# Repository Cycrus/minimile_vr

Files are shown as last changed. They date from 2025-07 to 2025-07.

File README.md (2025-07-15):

<div align="center">
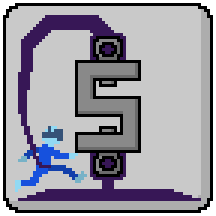
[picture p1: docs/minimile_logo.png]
SlimStep VR Logo
  
  <h1>SlimStep VR</h1>
  <h2>A Minimal, low-cost DIY VR treadmill system</h2>
</div>

<div align="center">
  
  
  
  
</div>

## What is SlimStep VR?
SlimStep VR is an answer to the demand for more affordable immersion enhancing VR devices. It is a minimal, low-cost VR treadmill system, which allows for more immersive smooth movement in Steam VR applications than a controller can provide.

You can mount the system to a wall or another sturdy part of your playspace. A rubber rope then connects your waist with the mounting point holding you approximately in space, while a sensor measures how much force you use to walk or run away from the mounting point. In addition to a slippery floor - or simply with wearing wool socks - the setup offers a rather immersive walking/running experience.

The system currently works unidirectional in the forward direction. In the current version there is no directional information implemented (left or right motion).

SlimStep VR is currently under active development.

## Installation
Installation requires setting up the driver software on your PC and setting up the hardware.

### Installing OpenVR Driver
The OpenVR driver is required for SteamVR to detect the device as an input option for VR games. Simply double click the file "install_driver.bat" in the folder "openvr_driver". It just takes an instant and the driver is installed.

If you want to uninstall the driver, there is a file named "uninstall_driver.bat" in the same folder.

> **WARNING**  
> In the current version it is important, that you uninstall the driver before you remove or relocate the project directory. Otherwise there will be some driver leftovers in the Steam registry, which could lead to undefined behavior. In all cases you can remove the driver with "<steam-directory>/steamapps/common/SteamVR/bin/win64/Vrpathreg.exe". Run it in the console with "show" as an argument to check the full path of the left-over driver, then run it with the argument "removedriver <full-driver-path>" to remove the left-over driver.

### Setting Up the Hardware
The more involved step is building the hardware of the system. You will need the following components. The links are links of the products I used for my own design.

- [50 kg load cell](https://www.amazon.de/dp/B077YLHG9D) (S-shape to measure pull forces, not push)
- Arduino (any type will do; I used an Arduino Nano Every) - For measuring the movement forces - Sends the load cell output to the PC
- [HX711 load cell module](https://www.amazon.de/dp/B0DJX8BPQL) - Required to read out the load cell
- [Tensioning belt](https://www.amazon.de/dp/B0DRNBRWLL) - Keeps you briefly in place while moving

<div align="center">
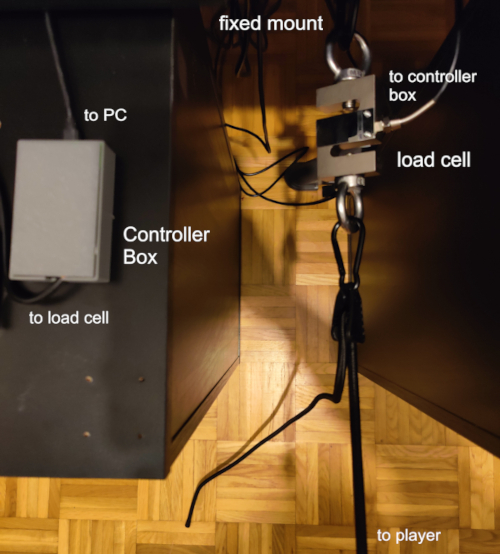
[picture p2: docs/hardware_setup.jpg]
Hardware Setup
  
</div>

For my design I used 2 M12 eyebolts and 2 carabiners to hang the load cell between my desk and the tensioning belt. I then knotted together the other end of the belt with some terry cloth to create a soft belt around my hip.

Now you need to wire the electrical components together as in the following image.

<div align="center">
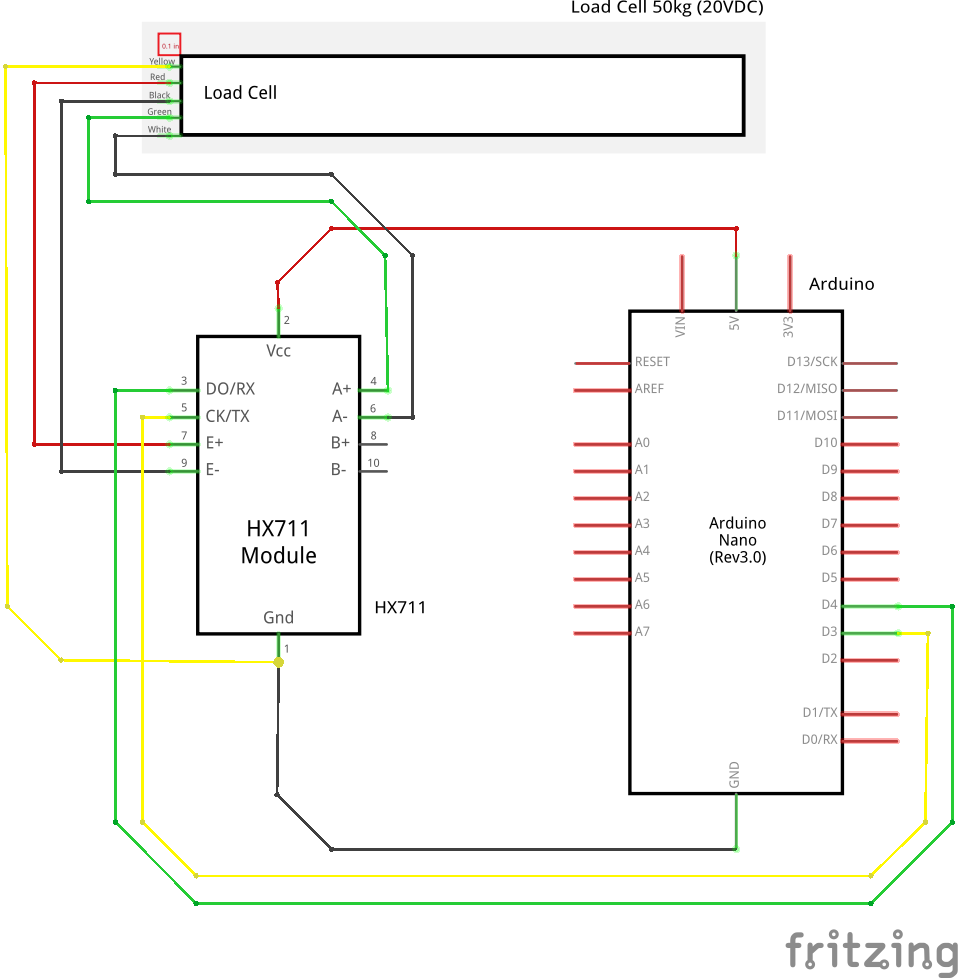
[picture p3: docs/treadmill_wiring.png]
Wiring
  
</div>

- Red wire: E+
- Black wire: E-
- Yellow wire: GND
- Green wire: S+/A+
- White wire: S-/A-

The HX711 then needs to be supplied with 5V from the Arduino. Connect its CLK (yellow) with D3 and its Data Out (green) with S4.

I used a 20VDC load cell to connect to my 5V excitation supply, wich worked perfectly fine.

After wiring everything, connect the Arduino to your PC with an USB cable. Now you need to upload the Arduino sketch "load_cell_module/load_cell_module.ino" to the Arduino. I suggest you use the official [Arduino IDE](https://www.arduino.cc/en/software/) for that. Compilation requires the HX711 Arduino library by Rob Tillaart.

> **Note**
> Additionally, the path "load_cell_module\case contains" stl and sliced gcode files to 3d-print a small case for the controllers. The lid of the case can be placed with double sided tape.

## Project Structure (Folders)
    - docs: Images of the project setup, wiring, etc.
    - load_cell_module: Contains everything regarding hardware.
      - case: Files for printing the case for the Arduino Nano and teh HX711 module
      - validation: Some Python scripts for validating the treadmill device
    - openvr_driver: Contains everything regarding the driver software.
      - CustomTreadmillDriver: The driver in its release shape
      - openvr_treadmill_driver_src: The source code of the treadmill driver

## References
  - OpenVR SteamVR driver documentation - https://github.com/ValveSoftware/openvr/wiki/Driver-Documentation
  - Finallyfunctionals OpenVR driver example - https://github.com/finallyfunctional/openvr-driver-example/tree/main

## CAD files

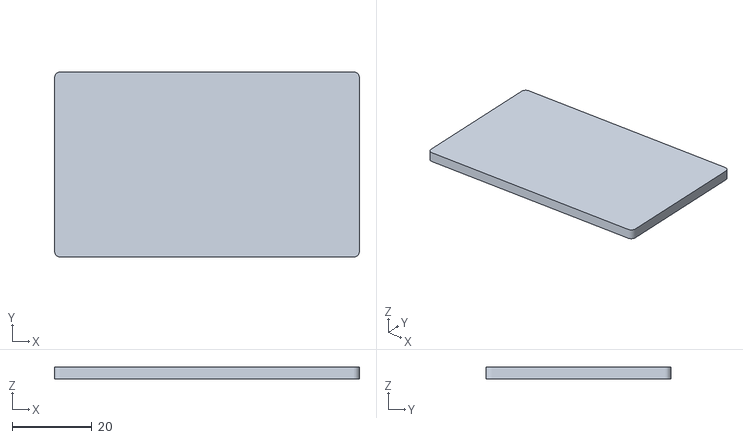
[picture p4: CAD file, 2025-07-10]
load_cell_module/case/treadmill_controller_case_top.stl
76.4 x 46.4 x 3.00

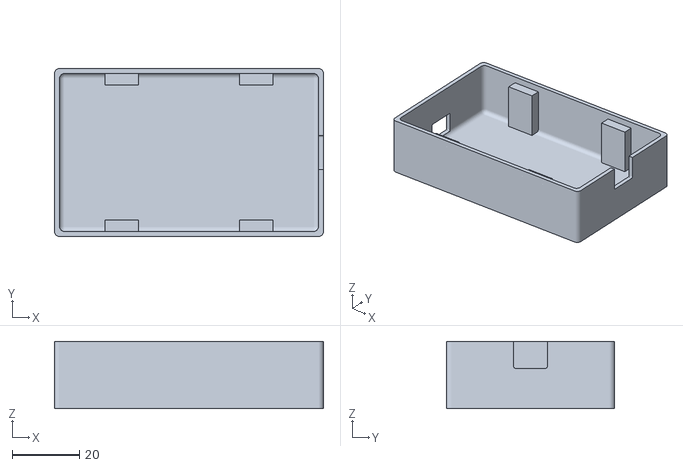
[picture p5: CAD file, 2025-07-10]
load_cell_module/case/treadmill_controller_case_bottom.stl
80.0 x 50.0 x 20.0

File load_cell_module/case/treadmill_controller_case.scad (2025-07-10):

// More information: https://danielupshaw.com/openscad-rounded-corners/

// Set to 0.01 for higher definition curves (renders slower)
$fs = 0.15;

module roundedcube(size = [1, 1, 1], center = false, radius = 0.5, apply_to = "all") {
	// If single value, convert to [x, y, z] vector
	size = (size[0] == undef) ? [size, size, size] : size;

	translate_min = radius;
	translate_xmax = size[0] - radius;
	translate_ymax = size[1] - radius;
	translate_zmax = size[2] - radius;

	diameter = radius * 2;

	obj_translate = (center == false) ?
		[0, 0, 0] : [
			-(size[0] / 2),
			-(size[1] / 2),
			-(size[2] / 2)
		];

	translate(v = obj_translate) {
		hull() {
			for (translate_x = [translate_min, translate_xmax]) {
				x_at = (translate_x == translate_min) ? "min" : "max";
				for (translate_y = [translate_min, translate_ymax]) {
					y_at = (translate_y == translate_min) ? "min" : "max";
					for (translate_z = [translate_min, translate_zmax]) {
						z_at = (translate_z == translate_min) ? "min" : "max";

						translate(v = [translate_x, translate_y, translate_z])
						if (
							(apply_to == "all") ||
							(apply_to == "xmin" && x_at == "min") || (apply_to == "xmax" && x_at == "max") ||
							(apply_to == "ymin" && y_at == "min") || (apply_to == "ymax" && y_at == "max") ||
							(apply_to == "zmin" && z_at == "min") || (apply_to == "zmax" && z_at == "max")
						) {
							sphere(r = radius);
						} else {
							rotate = 
								(apply_to == "xmin" || apply_to == "xmax" || apply_to == "x") ? [0, 90, 0] : (
								(apply_to == "ymin" || apply_to == "ymax" || apply_to == "y") ? [90, 90, 0] :
								[0, 0, 0]
							);
							rotate(a = rotate)
							cylinder(h = diameter, r = radius, center = true);
						}
					}
				}
			}
		}
	}
}

length = 80.0;
width = 50.0;
height = 20.0;
wall_thickness = 1.5;

mount_length = 10.0;
mount_width = 5.0;

loadcell_cutout_z_offset = 17.0;
loadcell_cutout_width = 10.0;
loadcell_cutout_height = 10.0;

usb_y_offset = 0.0;
usb_z_offset = 6.0;
usb_width = 10.0;
usb_height = 7.0;

// Box
module box_shape()
{
    union()
    {
        difference()
        {
            roundedcube([length, width, height], center = true,
                        apply_to = "xy",
                        radius = 1.5);
            translate([0, 0, wall_thickness])
            {
                roundedcube([length - 2 * wall_thickness,
                             width - 2 * wall_thickness,
                             height], center = true,
                             apply_to = "zmin",
                             radius = 1.5);
            }
        }
        for (sx = [-1, 1], sy = [-1, 1]) {
            translate([sx * length / 4, sy * width / 2 - sy * mount_width / 2 , 0])
                cube([mount_length, mount_width, height - wall_thickness*3], center = true);
        }
    }
}

module loadcell_cutout()
{
    translate([length / 2 + 0.1, 0, -height / 2 + loadcell_cutout_z_offset])
    {
        roundedcube([wall_thickness * 4, loadcell_cutout_width, loadcell_cutout_height], apply_to = "x", center = true);
    }
}

module usb_cutout()
{
    translate([-length / 2 - 0.1, usb_y_offset, -height / 2 + usb_z_offset])
    roundedcube([wall_thickness * 4, usb_width, usb_height], center = true);
}

// Box
difference()
{
    box_shape();
    loadcell_cutout();
    usb_cutout();
}

// Top
%translate([0, 0, 9])
{
roundedcube([length - wall_thickness*2.4, width - wall_thickness*2.4
    , 3], center = true,
                        apply_to = "xy",
                        radius = 1.5);
}

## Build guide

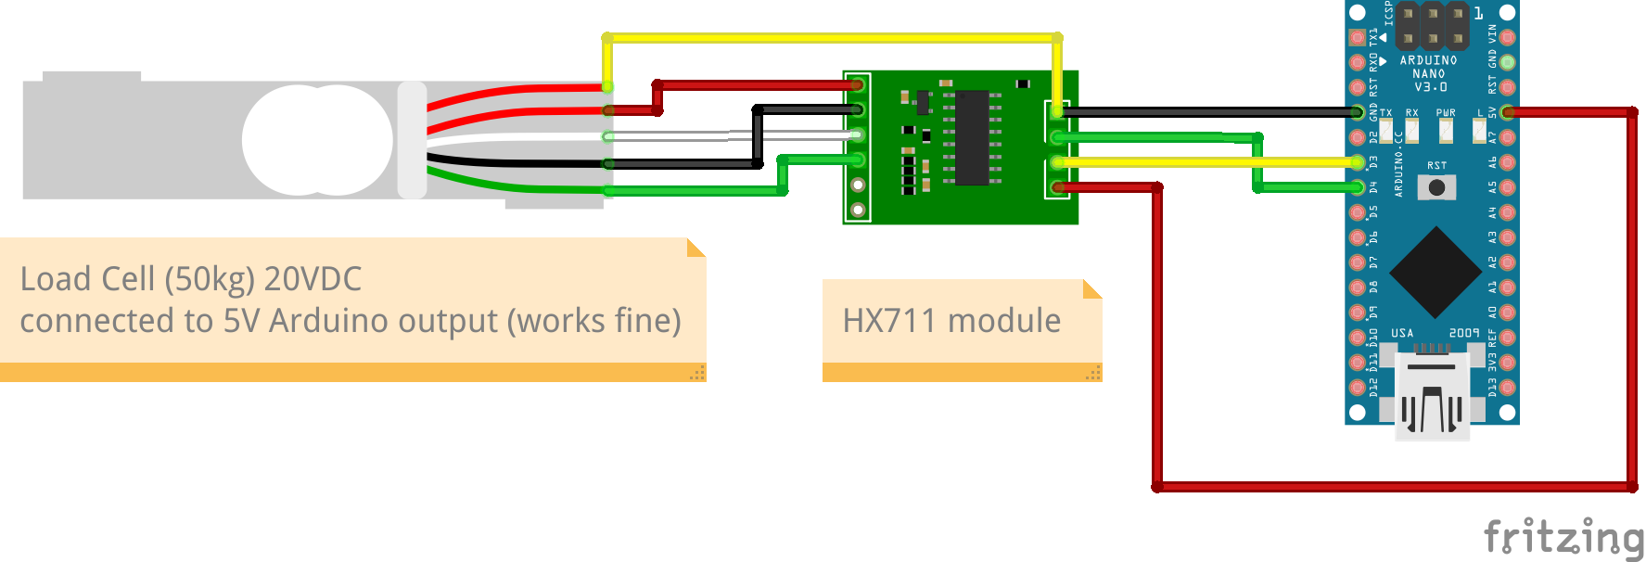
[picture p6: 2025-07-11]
docs/treadmill_wiring_bb.png

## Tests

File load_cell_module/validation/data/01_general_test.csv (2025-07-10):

value
0.00
35.00
26.00
2.00
17.00
15.00
-13.00
-33.00
-18.00
-3.00
-19.00
5.00
14.00
-4.00
-7.00
-10.00
-35.00
-15.00
-10.00
-8.00
0.00
4.00
32.00
43.00
-15.00
-25.00
-19.00
-16.00
-35.00
-64.00
-46.00
10.00
-22.00
-31.00
-14.00
77.00
439.00
1065.00
495.00
-824.00
-1617.00
-1998.00
-2334.00
-2769.00
-3097.00
-2827.00
-2540.00
-2337.00
-2412.00
-2186.00
-2198.00
-2547.00
-2710.00
-3399.00
-4373.00
-3023.00
-2238.00
-3049.00
-3018.00
-2490.00
-2810.00
80.00
1455.00
1559.00
3263.00
3301.00
2088.00
4641.00
4975.00
2108.00
1059.00
-1908.00
-4612.00
-5271.00
-7295.00
-7231.00
-6870.00
-6267.00
-5292.00
-4180.00
-2882.00
-2643.00
-2982.00
-3117.00
-4601.00
-6488.00
-6737.00
-7783.00
-8676.00
-8621.00
-8859.00
-8740.00
-8734.00
-8913.00
-8930.00
-8680.00
-8216.00
-7729.00
-6983.00
-6696.00
-6656.00
-6592.00
-6754.00
-6963.00
-6964.00
-7809.00
-7993.00
-9077.00
-9466.00
-9735.00
-9764.00
-9604.00
-9544.00
-9129.00
-8819.00
-8754.00
-8522.00
-9139.00
-7935.00
-8011.00
-11576.00
-7694.00
-8236.00
-9470.00
-7908.00
-7213.00
-8636.00
-8092.00
-7064.00
-7049.00
-8079.00
-8161.00
-6518.00
-6736.00
-6827.00
-2557.00
-451.00
-1514.00
-1429.00
-1541.00
-3830.00
-3453.00
-4963.00
-4793.00
-5316.00
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

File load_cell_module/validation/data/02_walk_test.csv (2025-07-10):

value
-14.00
-15.00
53.00
7.00
-12.00
-15.00
-45.00
-27.00
2.00
48.00
55.00
23.00
51.00
46.00
-3.00
-4.00
-14.00
-55.00
-55.00
-52.00
9.00
31.00
2.00
-45.00
-34.00
-6.00
-13.00
-22.00
0.00
260.00
632.00
-8.00
-913.00
-1611.00
-2084.00
-2106.00
-2388.00
-3052.00
-2974.00
-2841.00
-3042.00
-2882.00
-2803.00
-2604.00
-2186.00
-2153.00
-2348.00
-2504.00
-2582.00
-2905.00
-2692.00
-2600.00
-2307.00
-3057.00
-5327.00
-7311.00
-6559.00
-5712.00
-6253.00
-8525.00
-8853.00
-7943.00
-8183.00
-8823.00
-8697.00
-7994.00
-7712.00
-6903.00
-7422.00
-9762.00
-7546.00
-5891.00
-6654.00
-8743.00
-7648.00
-6544.00
-7664.00
-8819.00
-7574.00
-7007.00
-7799.00
-8067.00
-7525.00
-7535.00
-7672.00
-7560.00
-7538.00
-7728.00
-7942.00
-8686.00
-9037.00
-8134.00
-8174.00
-8629.00
-7991.00
-7664.00
-7329.00
-6944.00
-7419.00
-7073.00
-5211.00
-5563.00
-6883.00
-6468.00
-8279.00
-8617.00
-8981.00
-9838.00
-9718.00
-8495.00
-10633.00
-8546.00
-8340.00
-8839.00
-8569.00
-8444.00
-9026.00
-9423.00
-9526.00
-9997.00
-9914.00
-9331.00
-8983.00
-8756.00
-8568.00
-8645.00
-8653.00
-8599.00
-8131.00
-7610.00
-7116.00
-6466.00
-6208.00
-5356.00
-5271.00
-5100.00
-5643.00
-5402.00
-5853.00
-6207.00
-6650.00
-6748.00
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

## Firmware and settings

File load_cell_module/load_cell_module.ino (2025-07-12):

/**
 * The software running on the Arduino controlling the load cell.
 * Produces a 10 Hz output signal between 0 and 1 indicating how
 * string the load cell was pulled. This signal is interpreted
 * as different speeds of moving forward.
 * 
 * Compilation requires the HX711 Arduino library by Rob Tillaart.
 * The CLK pin of the HX711 is wired to digital 3 and the data output
 * is wired to digital 4 of the Arduino.
 */

#include "HX711.h"

uint8_t data_pin  = 4;
uint8_t clock_pin = 3;
HX711 treadmill;

float raw_measurement(float value)
{
  return value;
}

float ema_measurement(float value, float alpha)
{
  static float result = NAN;
  if(isnan(result))
  {
    result = value;
  }
  else
  {
    float prev_result = result;
    result = alpha * value + (1 - alpha) * prev_result;
  }
  return result;
}

float normalize_measurement(float value, float min_value, float max_value)
{
  float result = (value - min_value) / (max_value - min_value);
  if(result > 1.0)
    result = 1.0;
  else if(result < 0.0)
    result = 0.0;
  return result;
}


void setup()
{
  treadmill.begin(data_pin, clock_pin);
  Serial.begin(9600);
  while(!Serial) {}
  treadmill.set_scale();
  treadmill.tare();
}

void loop()
{
  float raw_value = treadmill.get_units();
  /*
  This is an active decision against smoothing. A useful EMA smoothing would lead
  to too much latency for a useful game input device.
  */
  // float smoothed_value = ema_measurement(raw_value, 0.07);
  float normalized_value = normalize_measurement(raw_value, 100000.0, 800000.0);
  Serial.println(normalized_value);
}

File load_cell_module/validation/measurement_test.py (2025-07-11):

"""
Reads the serial port and saves its input into a csv file.
Used to check the output measurements of the load cell device.
"""

import serial
import time

if __name__ == "__main__":
    ser = serial.Serial("COM3", 9600, timeout=1)
    filename = "load_cell_data.csv"

    with open(filename, "w") as file:
        print("Logging serial data. Press Ctrl+C to stop.")
        try:
            while True:
                if ser.in_waiting:
                    line = ser.readline().decode("utf-8", errors="ignore").strip()
                    print(line)
                    file.write(line + "\n")
        except KeyboardInterrupt:
            print("\nLogging stopped.")
        finally:
            ser.close()

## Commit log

2025-07-10 [LoadCellModule] feat: Added files for arduino software, wiring schematics, and 3d printable case.
    [01_general_test.csv, 02_walk_test.csv, 03_run_test.csv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]
2025-07-10 [OpenVrDriver] feat: Added files for driver skeleton. No functionality yet implemented.
2025-07-10 [OpenVrDriver] feat: Started implementation of serial connection to arduino.
2025-07-11 [OpenVrDriver] feat: Driver now receives serial data from treadmill device.
2025-07-11 [OpenVrDriver] feat: Implemented auto reconnection when device is lost.
2025-07-11 [OpenVrDriver] fix: Adapted input mapping, added legacy input mappings, and tweaked around some quirks of the OpenVr SDK. Also added uninstall driver script.
    [load_cell_data.csv]
2025-07-11 docs: Replaced wiring diagram with more precise version.
    [treadmill_wiring.fzz]

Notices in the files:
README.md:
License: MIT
